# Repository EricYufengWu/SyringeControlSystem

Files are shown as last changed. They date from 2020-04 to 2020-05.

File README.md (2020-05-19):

# Syringe Control System for Soft Robot Actuators

Demo

## General Info

This repository hosts code, PCB designs, and other results from my undergraduate independent research course. This research is supervised by Professor Chris Rogers at Tufts University.

The goal of the research is to develop a low-cost, modular pneumatic system that controls soft actuators using a linear actuator and a medical syringe. If time allows, I will also try to perform a well-rounded comparison between my new system and traditional controlling methods like [this one.](https://softroboticstoolkit.com/book/control-board). For now, the system is named "Syringe Control System", or SCS in short.

I would like to thank Professor Chris Rogers, Part-time Lecturer Brandon Stafford, and many other people from [Tufts Center for Engineering Education and Outreach](https://ceeo.tufts.edu/) and [Tufts Nolop FAST Facility](https://nolop.org/) for making this project possible.

Scroll down for pictures, demos, and complete building instructions.

Questions? Email yufeng.wu@tufts.edu and I will try to get back to you ASAP. I would also love to hear feedback or suggestions on how I can improve the current system.

## Images & Demos

Check out my presentation video on Youtube: https://youtu.be/lQ8lNfzFreA

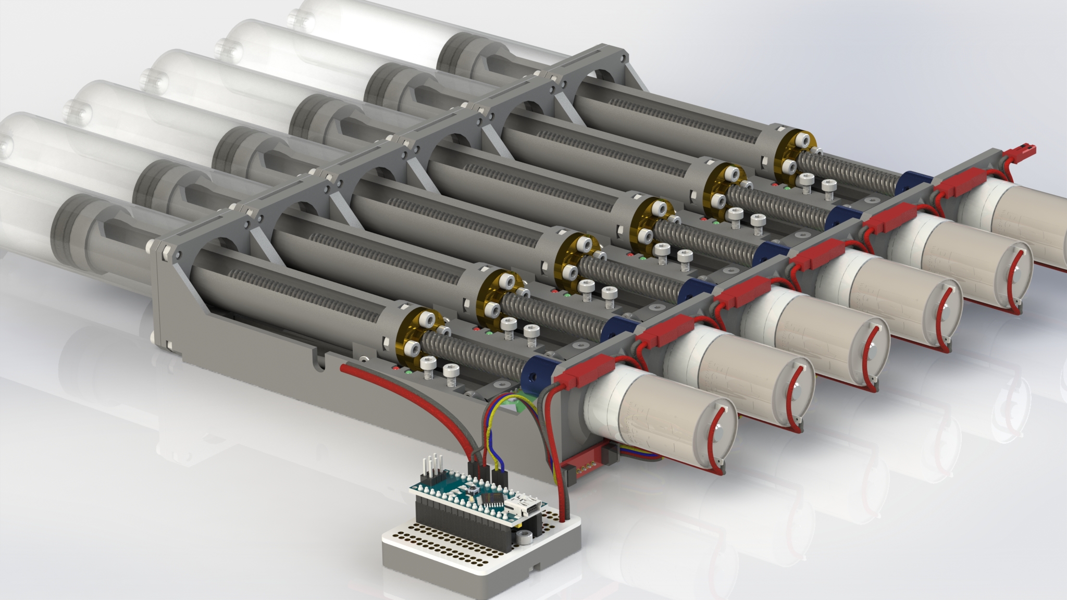
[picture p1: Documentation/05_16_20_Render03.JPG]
Rendering 01

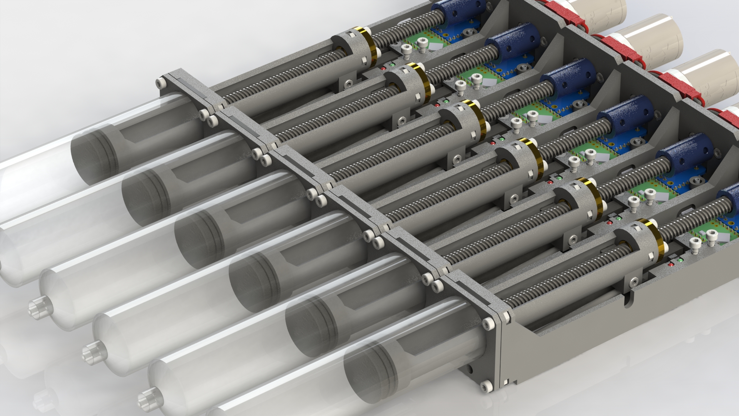
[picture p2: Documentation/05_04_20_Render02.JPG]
Rendering 02

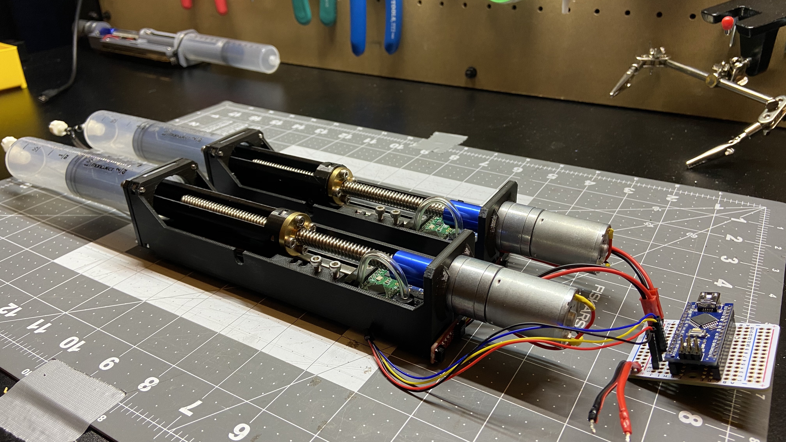
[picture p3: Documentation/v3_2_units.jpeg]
Working Demo


## BOM & Links

Click [here](https://docs.google.com/spreadsheets/d/1QlE3OmNmio2WvQ-pDKSaTucrADuNShoU5-5D75yimro/edit?usp=sharing) for the complete bill of materials.

Click [here](https://grabcad.com/library/linear-syringe-system-for-controlling-soft-robot-actuators-1/details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) for the 3D-printed components in STL, STEP, and SolidWorks format.

You can also view the 3D-model online through [here](https://autode.sk/2SUinZA)

Get the latest Gerber package and original KiCAD files (with custom libraries) under the "PCB" folder.

## Building Instructions

A full manual, including instructions on BOM, 3D-printing, ordering PCB, mechanical assembly, coding, and operation, can be found [here](https://github.com/EricYufengWu/PneumaticSyringeSystem/blob/master/Documentation/SCS_Manual_v3.1.pdf) in PDF. 

## Using The Code

Please see "Arduino_TeensyLC" for some simple demo code I wrote for the system.

Follow the instruction on the [PJRC Website](https://www.pjrc.com/teensy/teensyLC.html) to set up your Teensy LC. Similarly, go to the [Arduino Website](https://www.arduino.cc/en/Guide/ArduinoNano) if you are setting up an Arduino Nano as the Master Unit.

Upload "mid_master_TC" to the Teensy LC on each of your units. For every new unit, you will need to change the I2C slave address on line 41. If you are not sure what address values you can use, check out [this helpful list](https://learn.adafruit.com/i2c-addresses/the-list) form Adafruit. In the code, you can also tune the gain constants for the closed-loop control system in line 32 - 38. They have not been fine tuned yet, but for now they seem to work with little to no problem. If you end up finding better constant values, please do not hesitate to share it with me!

After you upload the code to a control unit, the unit should be operational in manual mode, i.e. after connecting the unit to 12V motor and 5V logic power, you should be able to control the unit using the built'in buttons. You should also be able to view the current pressure and positional data if you access the Teensy LC using a serial manitor on your computer.

Upload "top_master_nano.ino" to your arduino Nano as the master unit. You can use the serial input to send command to and get data from any designated unit in the I2C bus.

For more detailed instruciton, please refer to the instruction manual.

BEFORE YOU PROCEED: Please read the next section about the limitations of the SCS as well as things to keep in mind during its operation. 

## Limitations and Precautions
I2C protocol is capable of connecting more than 100 slaves at once. However, for the current version, it is recommended that you do not connect more than 8 units to the same master unit at the same time. This is due to the current rating of the wires used in the design. Future development will focus on how to tackle this issue.

Although the system uses Sparkfun's Qwiic system to communicaate with the units via I2C, it is currently NOT compatible with other boards on the Qwiic system: The SCS uses 5V on its logic line to power the Teensy LC, whereas the real Qwiic system uses 3.3V to power the sensors. Connecting other 3.3V sensors to the SCS system could permanently damage your sensors!

Keep in mind that although the system proves to be safe to operate, the stability of the system has not been so thoroughly tested. This mostly means that certain components might accidentally malfunction or get heated up.

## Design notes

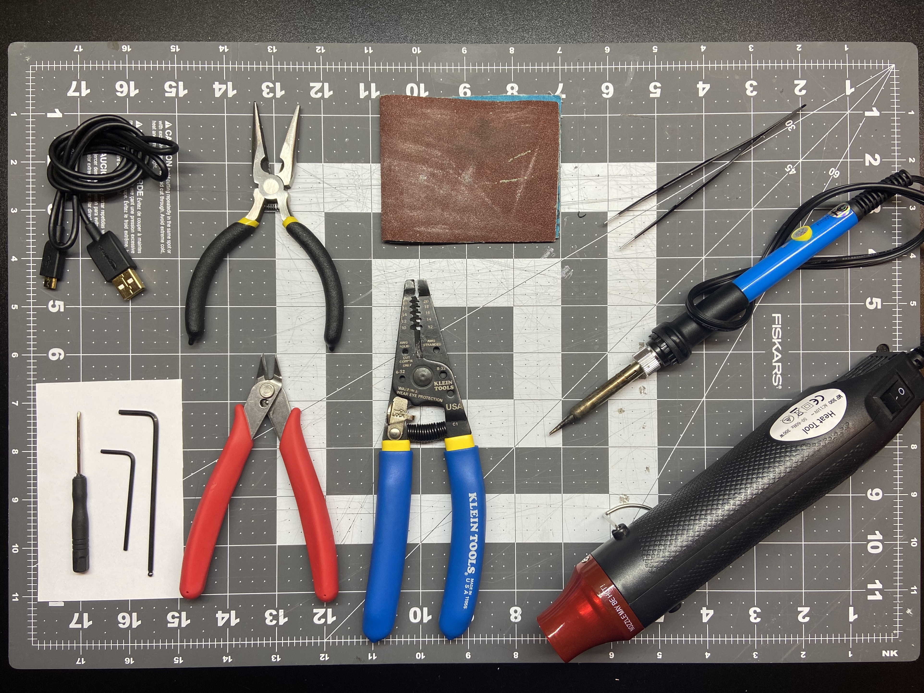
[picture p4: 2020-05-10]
Documentation/Tools_needed.jpeg

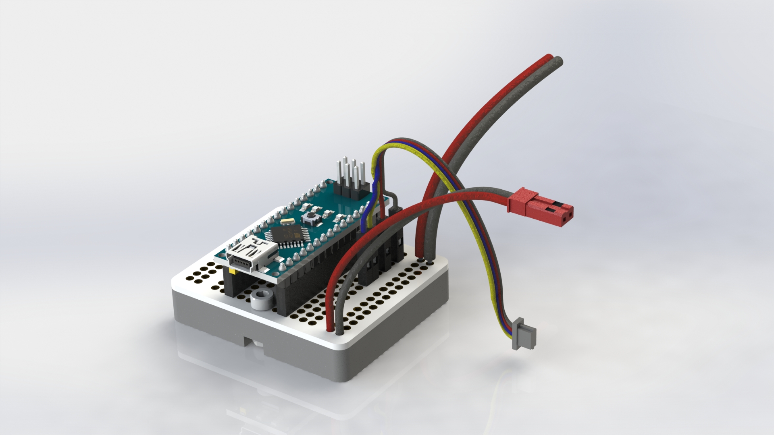
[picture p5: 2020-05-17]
Documentation/05_16_20_Render01.JPG

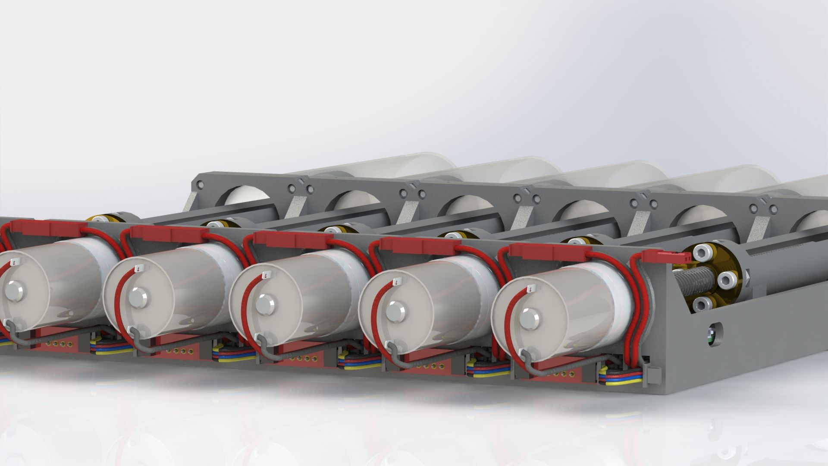
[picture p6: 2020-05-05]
Documentation/05_04_20_Render01.JPG

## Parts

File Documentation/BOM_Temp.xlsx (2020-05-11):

Item Name | Item Link | Unit Price | Item Qty | Total Price (No Shipping) | Total Price (4 units) | 500.86
Mechanical
12V motor MP #3227 | https://www.pololu.com/product/3227 | 19.95 | 4 | 79.8
4mm to 8mm shaft coupling | https://www.amazon.com/uxcell-Aluminium-Coupling-Connector-Electric/dp/B01B5QSIEW | 4.09 | 4 | 16.36
PLA filament | https://www.mcmaster.com/1317n73 | 45 | 1 | 45
M3 Flat Head 5mm | https://www.mcmaster.com/92125a125 | 3.89 | 1 | 3.89
M3 Socket Head 5mm | https://www.mcmaster.com/91292a110 | 4.97 | 1 | 4.97
M3 Socket Head 10mm | https://www.mcmaster.com/91292A113 | 4.97 | 1 | 4.97
M3 Socket Head 16mm | https://www.mcmaster.com/91292a115 | 5.87 | 1 | 5.87
M3 Hex Nuts | https://www.mcmaster.com/91828a211 | 5.55 | 1 | 5.55
M2 Button Head Screw 4mm | https://www.mcmaster.com/92095a451 | 4.12 | 1 | 4.12
Electrical
Teensy LC | https://www.digikey.com/product-detail/en/sparkfun-electronics/DEV-13305/1568-1233-ND/5721428 | 14.38 | 4 | 57.52
Motor Driver DRV8871 | https://www.digikey.com/products/en?mpart=3190&v=1528 | 7.5 | 4 | 30
Adafruit MPRLS Pressure Sensor | https://www.digikey.com/products/en?mpart=3965&v=1528 | 14.95 | 4 | 59.8
Short M-Header | https://www.digikey.com/product-detail/en/adafruit-industries-llc/4173/1528-2946-ND/10130488 | 0.75 | 6 | 4.5
Short F-Header | https://www.digikey.com/product-detail/en/adafruit-industries-llc/4174/1528-2947-ND/10130489 | 1.25 | 6 | 7.5
Linear Potentiometer | https://www.digikey.com/product-detail/en/tt-electronics-bi/PS100-2B1AR10K/987-1407-ND/2620676 | 5.49 | 4 | 21.96
Mini Push Buttons | https://www.pololu.com/product/1400 | 0.99 | 2 | 1.98
Right Angle M-Header | https://www.pololu.com/product/967 | 0.99 | 1 | 0.99
Qwiic I2C Breakout | https://www.sparkfun.com/products/14495 | 1.5 | 5 | 7.5
Qwiic to M-Jumper | https://www.sparkfun.com/products/14425 | 1.5 | 1 | 1.5
Qwiic 50cm Cable | https://www.sparkfun.com/products/14426 | 0.95 | 5 | 4.75
Green LED 3mm | https://www.sparkfun.com/products/9650 | 0.35 | 1 | 0.35
Red LED 3mm | https://www.sparkfun.com/products/533 | 0.35 | 1 | 0.35
Resistor 100 ohm | https://www.sparkfun.com/products/14493 | 1.2 | 1 | 1.2
Resistor 330 ohm | https://www.sparkfun.com/products/14490 | 0.95 | 1 | 0.95
16 AWG Wire | https://www.amazon.com/TYUMEN-Electrical-Extension-Flexible-Lighting/dp/B07SG23DT1 | 17.99 | 1 | 17.99
20 AWG Wire | https://www.amazon.com/BNTECHGO-Silicone-Flexible-Strands-Stranded/dp/B01F8PO5XE | 11.99 | 1 | 11.99
Heat Shrink Set | https://www.amazon.com/560PCS-Heat-Shrink-Tubing-Eventronic/dp/B072PCQ2LW | 7.99 | 1 | 7.99
PCBs | https://oshpark.com/ | 45.4 | 1 | 45.4
Pneumatic
Syringe | https://www.mcmaster.com/7510a802 | 3.13 | 4 | 12.52
Male Luer to 3/32'' | https://www.mcmaster.com/51525k212 | 3.78 | 1 | 3.78
Female Luer to 3/32'' | https://www.mcmaster.com/51525k122 | 4.27 | 1 | 4.27
3/32'' Y connector | https://www.mcmaster.com/5463k52 | 7.96 | 1 | 7.96
3/32'' Tubing | https://www.mcmaster.com/5233k92 | 15 | 1 | 15
PTFE Sealing Tape | https://www.mcmaster.com/6802k18 | 2.58 | 1 | 2.58
Other Tools Needed
Breadboards
Jumper Wires
Multi-meter
Heat Gun
Soldering Station
Wire Cutters
Precision Plier
Flush Cutter
X-Acto Knife
Benchtop Power Supply
Sand Paper
Screw-drivers or Allen Keys
3D-printer
Some Wires

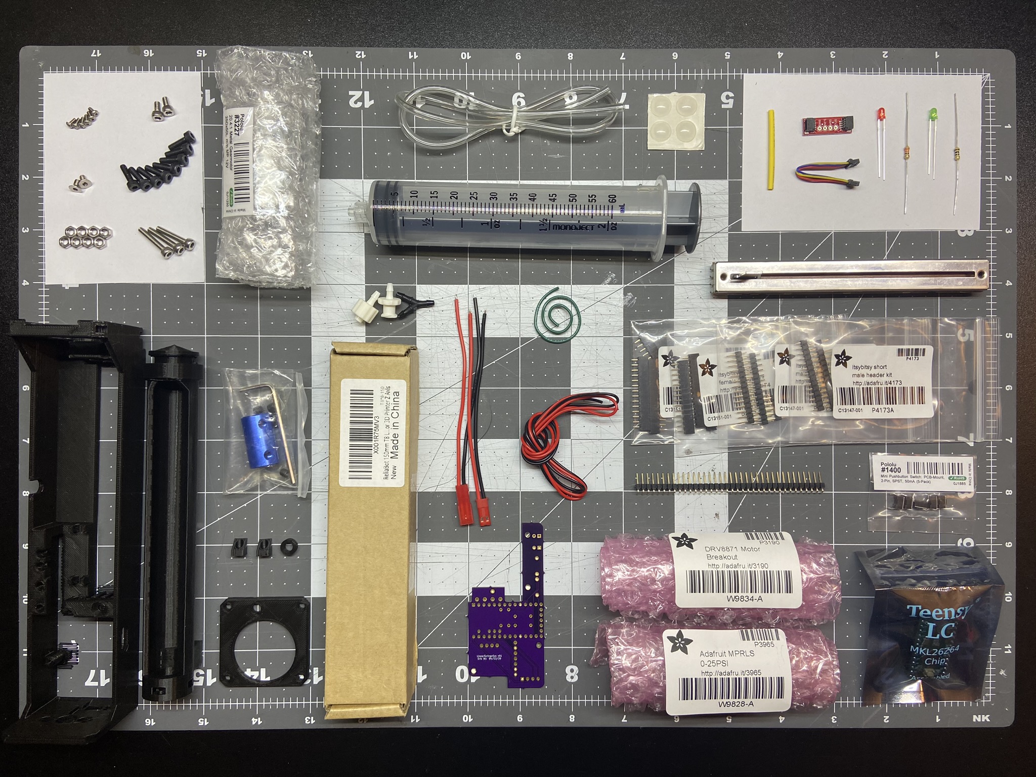
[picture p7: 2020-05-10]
Documentation/Material_1.jpeg

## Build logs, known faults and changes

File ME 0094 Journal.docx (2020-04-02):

Jan 14th, 2020

Rough Plan:

- Step 1: LEGO actuator + small syringe,
  - powered by LEGO Technic block with simple forward/reverse option
  - manual air release with switch
  - goal: explore possibility of using low-cost, easily-accessible components to control soft robot actuators.
- Step 2: Stepper motor + medium/large syringe
  - Powered by Arduino/raspberry pi with ability to hold at exact position
  - Manual/automatic air release
  - Pressure sensor in line & display readings or become part of the control algorithm
  - Goal: to produce more stable and precise pressure output
- Step 3: Compare step 1 & 2 with existing control system (pump + solenoid valves)
- Step 4: using step 1 or step 2 to create a demo with multiple channels (snake, tentacle, articulated fingers etc.)
- Step 5: (if time allows) ultimate strength challenge
  - Fabricate a custom syringe at Bray (aluminum etc.)
  - Use a heavy-duty linear actuator with feedback
  - Test the performance on an artificial air muscle

To do: Look up ferromagnetic materials

Links:

LEGO Linear Actuator: https://www.amazon.com/Lego-Technics-Linear-Actuator-61927C01/dp/B014T9E43G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

Stepper motors:

Heavy-duty Linear Act.: https://www.pololu.com/category/127/linear-actuators

Syringes:

Pressure Sensor:

Jan 22nd, 2020

- Performed research on existing control mechanism for soft actuators.
  - In most cases, hard valves and pumps are still widely used for controlling soft actuators:
    - https://softroboticstoolkit.com/book/control-board

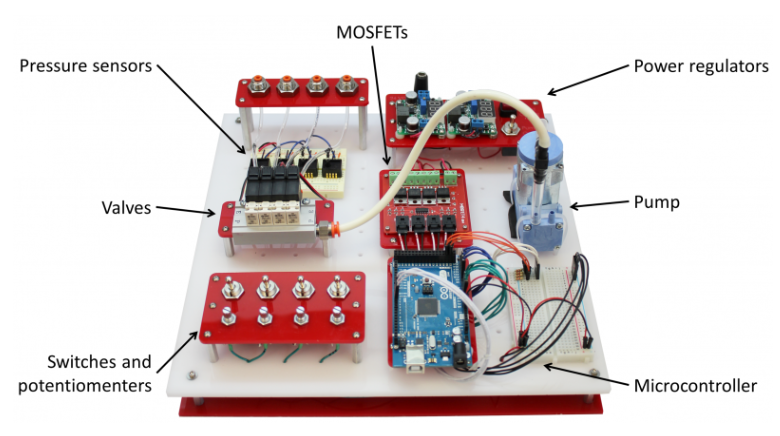
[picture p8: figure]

This is a traditional control system presented by Soft Robotics Toolkit and is open-source. Similar set up is also used by NASA: https://www.nasa.gov/feature/langley/beyond-the-metal-investigating-soft-robots-at-nasa-langley

  - A research group recently published a paper about making a custom-made, soft, bistable valve to replace the hard solenoid valves: https://robotics.sciencemag.org/content/3/16/eaar7986/tab-pdf
  - Useful paper that summarizes current soft robotics manufacturing and control systems: https://www.nature.com/articles/nature14543.pdf
  - ***Found this useful research paper on using force-feedback and the pressure-feedback controllers to actuate the SRAs reliably. https://www.ncbi.nlm.nih.gov/pmc/articles/PMC6545483/pdf/nihms-1027456.pdf

Based on research, it seems a promising direction for my research is to build a syringe pneumatic/hydraulic system that uses force-feedback or pressure-feedback controllers to actuate soft robot actuators.

**Q Has anyone used the linear actuator with EV3?

- Submitted purchase request for some LEGO linear actuators
- Next Steps:
  - build the actuator in LEGO version
  - review the research paper and learn control
  - start designing version one of my syringe system and produce a BOM

Jan 26th, 2020

- Found this 3d-printed linear rail for syringes - https://www.youtube.com/watch?v=Q3A4NqTPOYY

Might be useful as reference when I design my setup.

Jan 27th, 2020

- Used a linear actuator, The MINDSTORMS EV3 kit, and a syringe to build a prototype setup for the LEGO version of the system. The linear actuator is directly mounted to a LEGO medium motor, which is then controlled by the brick with VSC and micro-python.
- The setup was able to control the linear motion of the syringe to some degree, however:
  - The structural integrity of the LEGO build and the torque provided by a single linear actuator is not ideal. The next step could be to mirror the build at the opposite side with another linear actuator to double the force and make the setup Stabler.
  - The LEGO linear actuator does not have a large stroke width. Will need to try with actuators to confirm this.

Jan 30th, 2020

- Found a research journal about developing a soft robot using ferromagnetic materials: https://www.researchgate.net/publication/335455581_Ferromagnetic_soft_continuum_robots
- Reason not to focus in this direction:
  - Not realistic with current available resources, time, and scope of the independent studies
  - Focuses more on developing new types of actuation methods, whereas I’m planning to focus on improving the control method for existing, accessible, and easy-to-fabricate materials.
- Finished building the LEGO version of the syringe system with two medium motors and two linear actuators.
  - Able to control the syringe to actuate some actuators in a reasonably accurate manner
  - Proved that LEGO can control soft robotics!
- Next steps:
  - Improve/Document the current LEGO setup
  - Start designing a non-LEGO version, give design&BOM

Feb 5th, 2020

- 80% done with the Instructables on making the LEGO syringe system. Still waiting to cast a successful soft actuator and film a demo of the complete system.

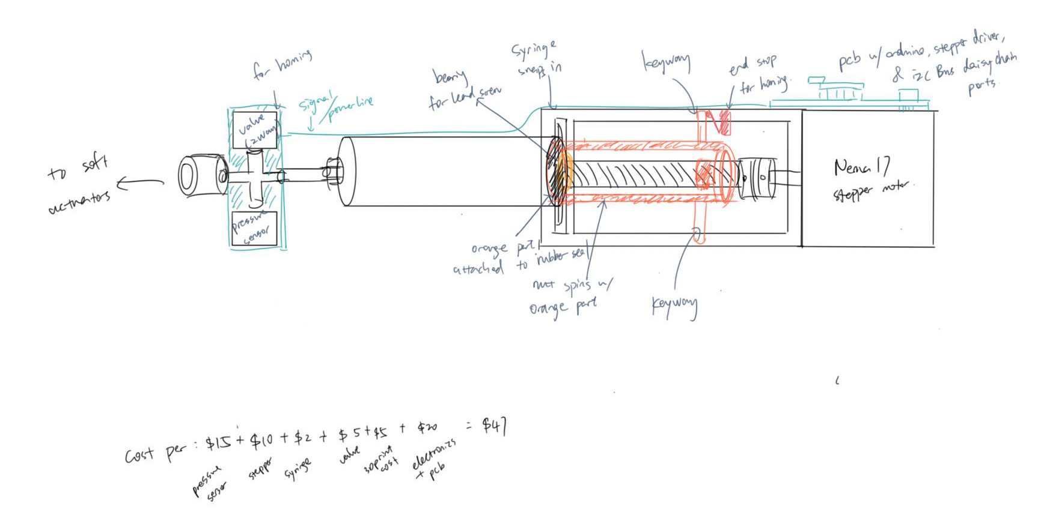
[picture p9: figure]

- Preliminary sketch done for the new, non-LEGO syringe linear actuator system:
  - Trying to limit the cost of each unit to be less than $50.
  - Ideally, each unit should have a microcontroller on board, capable of listening to an I2C bus – modularity.

Feb 9th, 2020

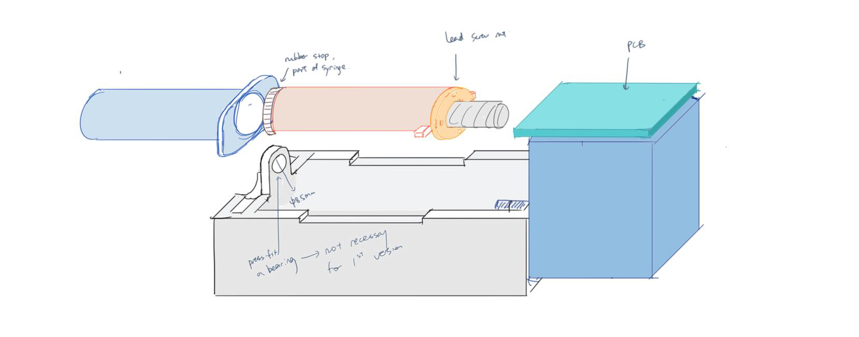
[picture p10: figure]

- Detailed Sketch
- BOM:
- Preliminary CAD with selected components:
  - Included stepper motor, shaft coupler, lead screw with nut, and syringe components

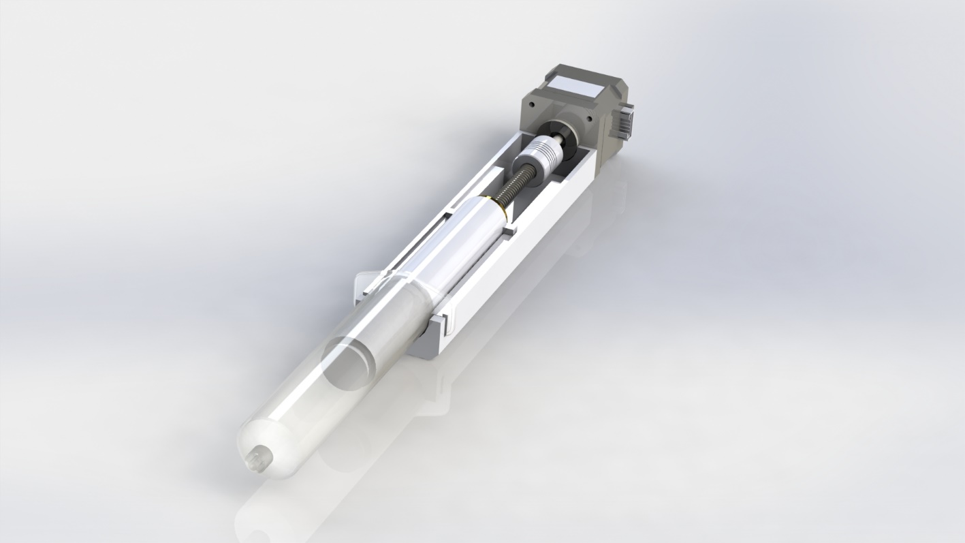
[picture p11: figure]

  - still need to add: end stop, tubing, upper shell, PCB, etc.

Feb 18th, 2020

- First Iteration of the linear actuator model has some issues:
  - It is difficult to put in the screw that are used to attach the stepper motor to the main housing
  - The syringe lip was a little loose when attached
- Updated the CAD model in SolidWorks, and hopefully I can print the next version soon.
  - I was also trying to incorporate end stops to the bottom_housing model. Found this compact end stop module made for 3D printers, but will suit my purpose:

https://www.amazon.com/Printer-Accessories-Mechanical-Endstops-MXRS/dp/B083BZ3VTL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

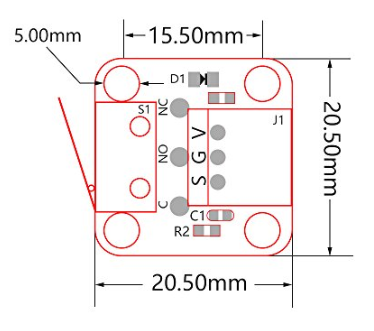
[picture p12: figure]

This end stop converts touch sensor data to digital high, so I can directly plug it in a micro-controller, no need for pull-down resistor.

Feb 22nd, 2020

- 3D-printed out and assembled the first version of the syringe system. Assembled the components – except for the end stop and the pressure sensor, which I’m still waiting for to arrive in a few days. Right now, the system looks pretty good. Some following steps:
  - Connect the end stop module, pick a stepper motor driver, and breadboard the electronics for testing the syringe
  - The end support for the lead screw appears to be a little tight. Consider inserting a bearing or simply increase the diameter for the next iteration.
  - Design a 4-way connector that will be attached to the end of the syringe, which allows connection to a valve, a pressure sensor, and the actuator.

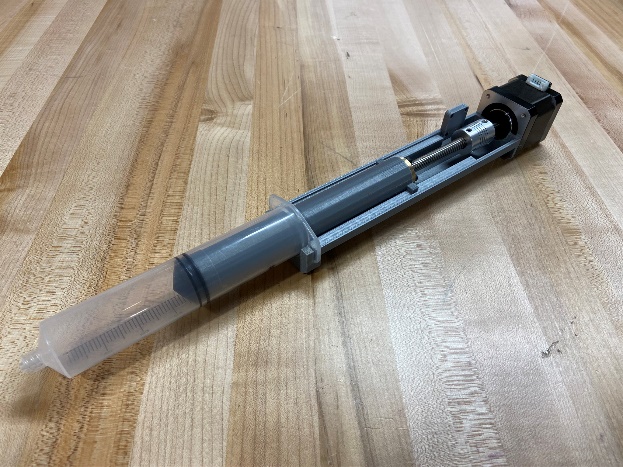
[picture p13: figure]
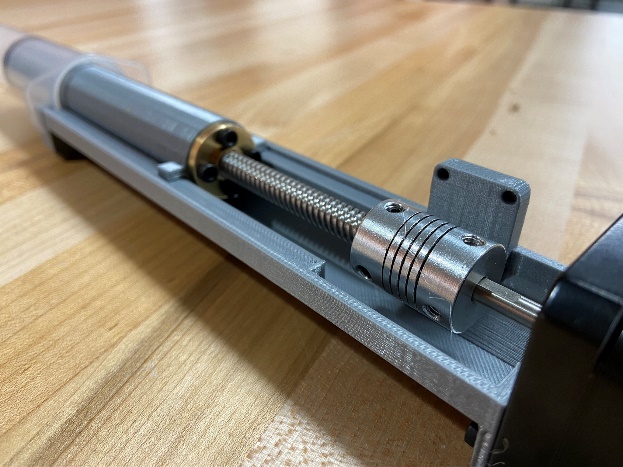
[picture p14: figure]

Feb 27th, 2020

- The pressure sensor, solenoid valve, and the end stops have arrived. Some issues that are currently preventing me from moving forward:
  - The end stop does not fit in the assembly the way id did in SolidWorks – the solder joints are thicker than my estimation. Will have to make changes in the design, moving the module to another location
  - The pressure sensor and the solenoid valve are a little bigger than I expected. Will see if I can still incorporate them while maintaining the modularity of each units.
- Now that I’m starting to think about controlling the motor, here’s a qualitative schematic

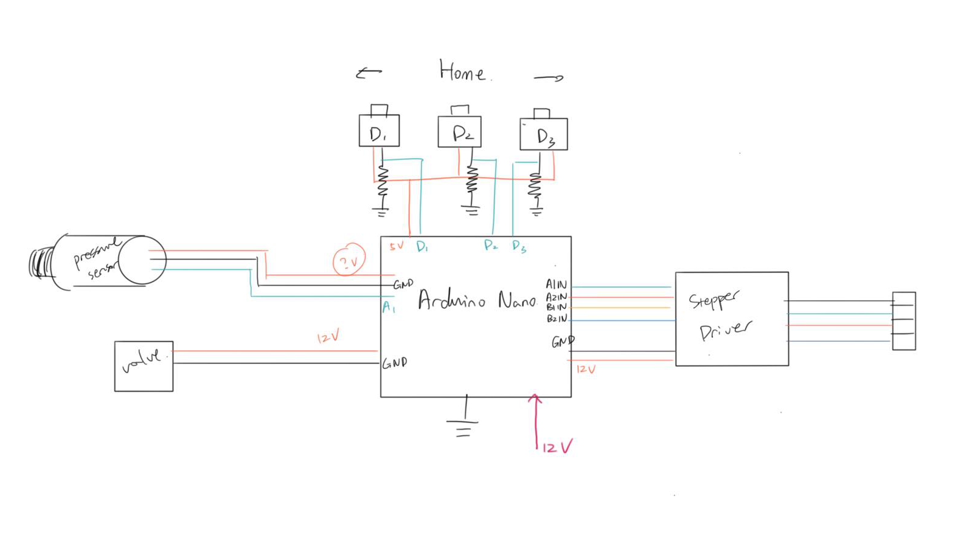
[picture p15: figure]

March 3rd 2020

- Second version of base body: End stop fits in, but the flanged nut would hit the main switch body, deforming the touch switch before the switch can be activated. Solution: Modeled in an attachment piece onto the middle piston, so the piston will flush with the flange.
- The top attachment to the stepper motor forms an angle relative to the base-added another screw from bottom of the base to connect the two components together
- My plan for the following weeks:
  - Finish making a single model
  - Reach out to Steve Cogger (through Chris) after having the system tested on a breadboard.
    - Will need to decide between usb serial and I2C. Leaning towards I2C because the need to stack the modules together, and expand the possibility for advanced users to customize and integrate the system to their existing Arduino/hardware projects
  - Develop testing protocols to compare a single syringe module and a valve system
    - Compare the time response of both models
    - Noise level at performing specific tasks (e.g. incrementing pressure steps, holding at a specific pressure level, etc.)
    - Operation to failure of valves vs syringes (for valve – limited lifetime, for the syringe – likely to be much longer)
    - Maximum pressure output (might be more of a challenge to the syringe system
    - …

March 5th, 2020

- 3D-printed and assembled the next iteration of the end stop + base + lead screw. Below is a series of images showing the assembly design:

Had to print an extra extension piece to make the center piston align with the end of the flanged lead screw nut, so that the end stop will fully engage at the current position.

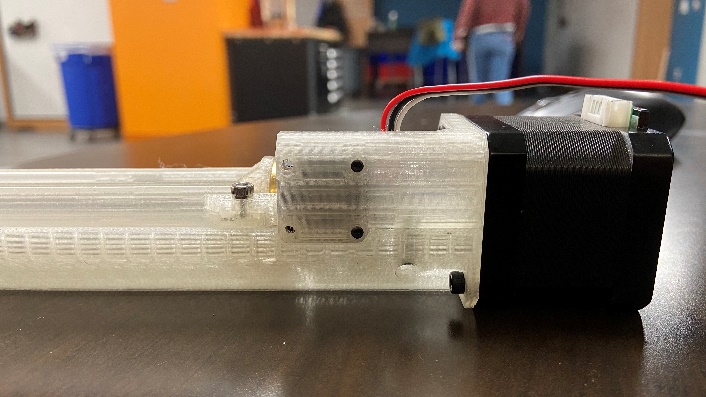
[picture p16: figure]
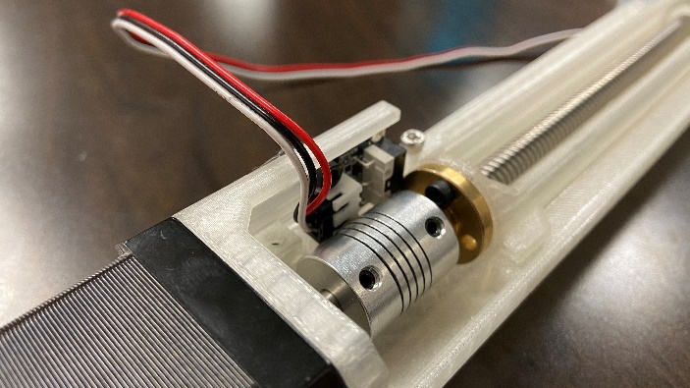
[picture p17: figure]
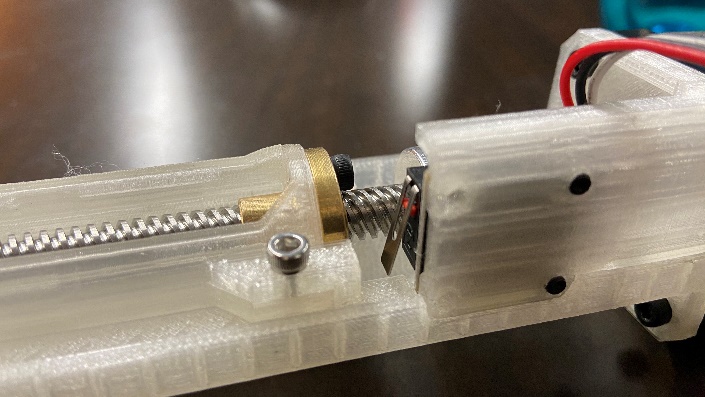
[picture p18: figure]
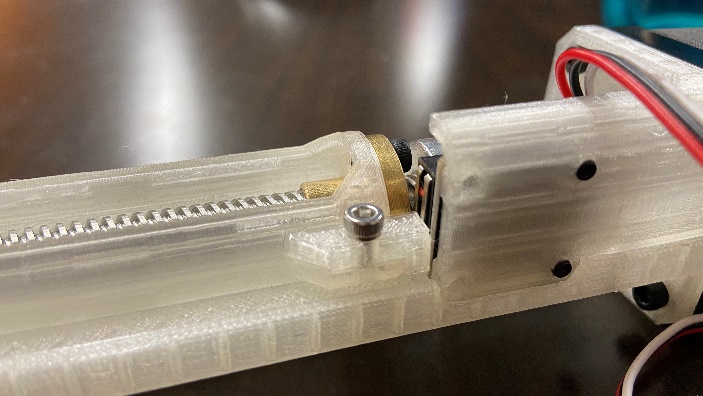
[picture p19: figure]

Chris also suggested that I try a linear potentiometer. I might look into buying one to test it out, but there are a few concerns I have regarding the linear pot:

  - The size of the linear potentiometers is rather fixed – might be a little too big for the current design
  - Length – again, might end up too long/too short
  - One way to solve the last two issues is with a custom-made linear potentiometer, but it might end up not being as reliable and will take up longer time.

March 9th, 2020

- Found a different type of pressure sensor:
  - Link: https://www.digikey.com/product-detail/en/nxp-usa-inc/MPXV7002DP/MPXV7002DP-ND/1168436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
  - Advantage: compact and relatively cheap. Available on digikey as an SMD part. Might ask Chris to order one to play with and see if this can replace the big, bulky pressure sensor
- As for update regarding the solenoid valve and how it can be integrated:
  - Considering to instead have the 3d-printed piece have a hose nozzle output, so that users can decide whether they want a cheap manual valve or an integrated solenoid valve (will leave a place for the valve control in the pcb.)
  - Next is to perform iteration on 3d printers to find the optimal tolerance for luer lock and other related dimensions

March 10th, 2020

- Rapid prototyping on the Prusa MK3S 3D printer resulted in a working model of low-cost luer lock.
- Found a possible alternative to the solenoid valve system: 4-way stopcock:

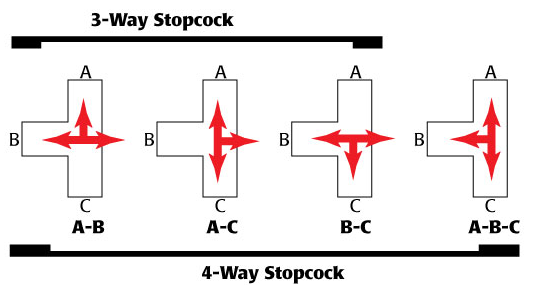
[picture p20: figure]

Possible vendors:

https://www.vitalitymedical.com/hi-flo-four-way-stopcock.html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

https://serfinitymedical.com/products/discofix-stopcock-4-way-b-braun-456020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

  - As seen from the image, I could connect C to the syringe, and A to actuator + pressure sensor. Configuration #2 is the operation mode, and configuration #4 is the calibration mode.
  - For the final setup, this could be a simple add-on to the system. The user can choose to directly connect the 3D-printed connector I designed that splits into the actuator and pressure sensor connection; alternatively, they could choose to purchase this and simply add the 4-way stopcock inline to make the calibration process easier to perform.

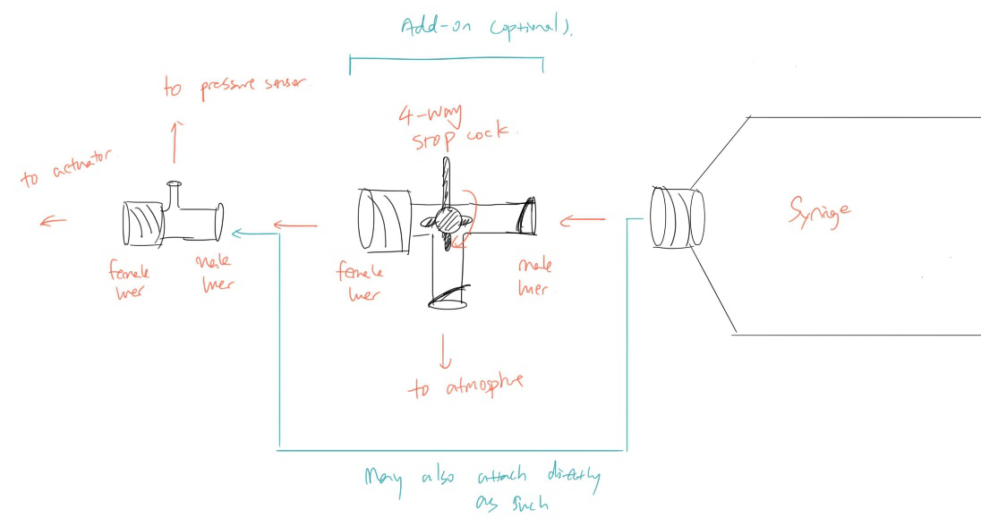
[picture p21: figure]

- Considering bringing back the Adafruit I2C pressure sensor – other options are wither two clumsy, too expensive, or does not have desirable pressure range.
  - Will validate this decision by testing the Adafruit pressure sensor and the NPT pressure sensor with the gripper actuator
- * Top priority is still finishing the open-loop system with the stepper motor and the syringe.

March 11th, 2020

- Campus will shutdown doe to Coronovirus. Will need to come up with a plan

Week of March 9th | Finalize the physical design the best way I can Try and solve the stepper motor vibration issue Breadboard manual control system with buttons
Week of March 16th | Take some rest…? Use the manual control system to test out different pressure sensors. Pick a pressure sensor.
Week of March 23rd | (if needed, figure out soft I2C/ possibility to use an Arduino as both a master and a slave)
Week of March 30th | Close-loop system with pressure sensor in line with syringe and actuator
Week of April 6th | Continue working on single close-loop system Start developing I2C code for master Arduino/Pi and individual Arduinos.
Week of April 13th | Continue developing I2C code for master Arduino/Pi and individual Arduinos.
Week of April 20th | Acquire performance data and compare with air pump.
Week of April 27th | Acquire performance data and compare with air pump. Organize research results and prepare for potential presentations.
Week of May 4th

Will mostly need (and might be able to get):

A soldering station

Jumper wires, resistors, capacitors, other electronics. Various pre-made boards from Adafruit/Pololu etc.

PCB manufacturing service

Nscope

March 21st, 2020

- A little behind the schedule, mostly dealing with COVID-19 related issues. Hope to resume research starting today.
- Revisited previous breadboard setup where the stepper motor is vibrating and creates unpleasant sound.
  - Tried adding different capacitors to reduce current spikes
  - Searched online to try to find solutions
  - Reduced some vibration noises by applying hot glue to loosen parts on the end stop module
  - Considering replacing the flexible shaft coupling to spider-style/normal coupling to reduce noise and size. Some viable options include:
    - https://www.amazon.com/ZYCST-Aluminium-Coupling-Connector-Airplane/dp/B07QPKGM1Q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
    - https://www.amazon.com/Befenybay-Aluminium-Flexible-Coupling-Connector/dp/B07RMZCLZ3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
- The stepper motor, unfortunately, was not delivering enough torque. It started skipping once out of a few steps as pressure increases. It still pushed the syringe all the way to the end, but skipping steps made it hard to monitor the position. Possible solutions I can think of:
  - Ignore the step-skipping, and use a linear potentiometer to monitor the position
  - Use a stronger stepper motor
  - Use a DC motor with encoder (or without?) and use either two endstops or a linear potentiometer
  - Use a brushless motor…? Maybe see if O-drive has an open-source schematic…
- Motor RPM to linear actuator moving speed:
  - Lead screw: 2mm pitch, 4 starts
  - 1 revolution of motor – 8mm travel of lead screw.
  - Travel speed (mm/sec) = (RPM / 60) * 8mm
  - Current speed with 17HS19-2004S1: approx.. 16mm/s; therefore, to find a DC motor that matches the speed, I should be looking for a motor with RPM > 120. Ideally the higher the better, with enough torque and reasonable rated voltage and current draw.
- Next steps:
  - Prototype a connector with female luer, male luer, and a tube coming out – then hook up a pressure sensor in line with the syringe, and use a scale found in my house to graph a pressure-torque characteristic of the motor.
  - Pick a desirable maximum pressure and a corresponding force. Calculate the torque needed for the motor. Use this as the final criteria in selecting a motor (maybe with a factor of safety of about 1.5?).
    - https://www.pololu.com/category/115/25d-metal-gearmotors
    - https://www.pololu.com/category/116/37d-metal-gearmotors
  - Look for linear potentiometers (100mm travel length).
    - https://www.digikey.com/product-detail/en/tt-electronics-bi/PS100-2B1AR10K/987-1407-ND/2620676
    - Might need a larger syringe since the travel length is now limited: https://www.amazon.com/DEPEPE-Connections-Scientific-Measuring-Filtration/dp/B07PPFLKRD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

March 22nd, 2020

- Prototyping of the Y Luer connector hit a bottleneck – the pla isn’t strong enough and does not produce an air-tight environment. The pisture shows the iterations I performed today:

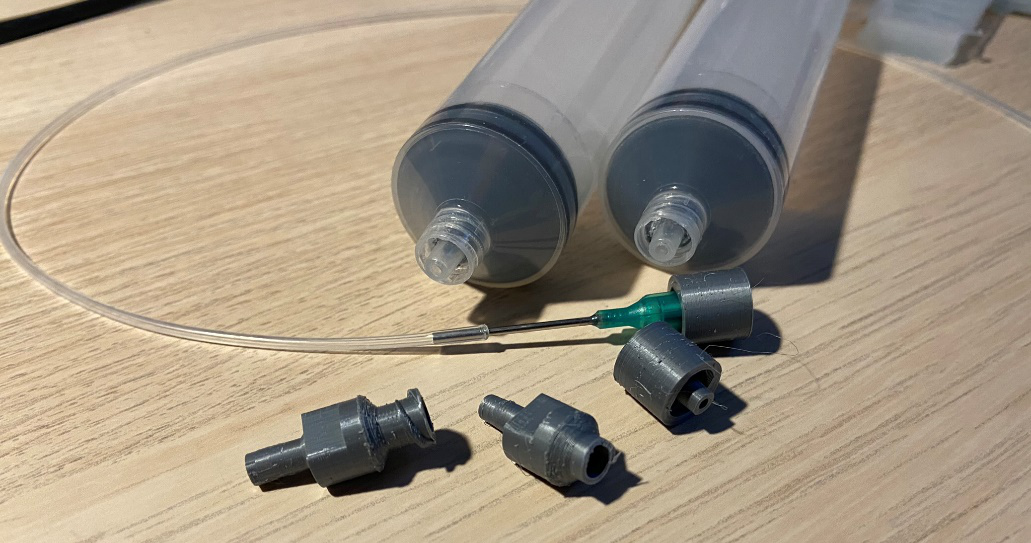
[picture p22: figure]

The PLA wasn’t strong enough – as I tried to untwist the connector off from the syringe, the end broke off and stayed inside the luer connector, making the syringe unusable.

Some options includes:

  - Teflon Tape
  - Use petg/or other PLA substitute
  - Use industrial Luer connectors instead (promising)

So the current plan would be:

  - Purchase some y-connector, and while waiting for the shipment, I could also purchase some PETG and Teflon Tape. In the best scenario, both methods would work and I can present more alternatives of my design in the final report. I hope that through this process, at least one of the options would work.
  - https://www.qosina.com/y-connector-male-luer-connector-with-spin-lock-two-female-luer-lock-ports-84044

https://www.mcmaster.com/51525k122

use 3/32 ID Tubing in the pressure line. Solved the problem!

- To do:
  - Start compiling an order list for CEEO
  - Use the scale to roughly measure the pressure-force relation
  - Use the relation to predict the force needed to actuate the example gripper design
  - Calculate the required force/torque of motor. Pick a new motor and re-design.

March 23rd, 2020

- 60ml Syringe Pressure-Force Characteristic Test. Method: I placed the end of the syringe on a kitchen scale, with the pressure sensor hooked up to the other side. Next to the setup, I have the Arduino Serial monitor opened, which outputs the pressure in the system in PSI.

YouTube Link (listed only): https://youtu.be/_aCKt8hK5S8

  - I chose to only graph results averaged from trial 4-6, since the frictionless syringe gives a much more linear result. The force required to get the pressure to 24 PSI (a little below the limit of the Adafruit pressure sensor) is around 39.12N.
  - I also did a test on the existing soft gripper I have by pressing the syringe to the kitchen scale in similar fashion. I performed 3 trials and ended up with a force output of around 19.77 N. From the characteristic graph, the pressure around 18.97 psi, which is well within the range of the pressure sensor.

March 25th, 2020

- Calculated the required torque based on the following video: https://youtu.be/cdDYhViYO9s

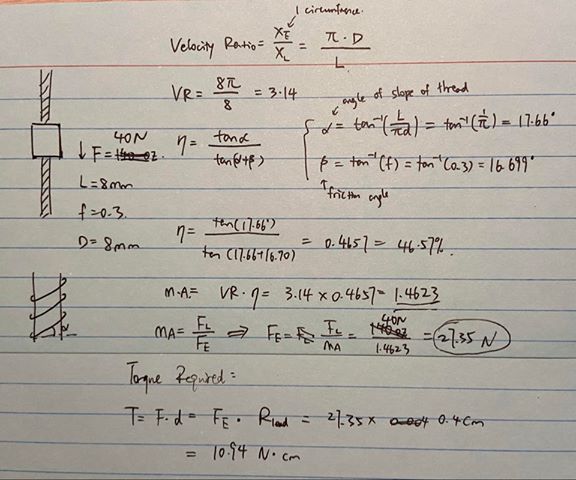
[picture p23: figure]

Interestingly, the calculation implies that only about 10.94 N*cm of Torque is needed, which is well within the “holding torque” of the stepper motor I am using. Therefore, I revisited the stepper motor setup.

  - I noticed that the friction inside the free-running syringe is partially the reason of the poor performance. I applied some cooking spray :) to the inner rubber seal and it worked a little better, but still not as close as the rated performance.
  - I then took a closer look at the driver and whether the driver is actually outputting enough current for the motor. Measuring the current through one coil gives approximately 600mA. From the A4988 Datasheet, it appears that this corresponds to a current draw of ~1A, which is less than the rated 2A of the stepper.

A4988 Datasheet: https://www.pololu.com/file/0J450/a4988_DMOS_microstepping_driver_with_translator.pdf

Pololu stepper driver instruction: https://www.youtube.com/watch?v=89BHS9hfSUk&feature=youtu.be

  - I then realized that the A4988 board I am using is different from the ones that Pololu sells – could be a knockoff, which prevents me from accurately measuring and adjusting the current limit. I already turned the on-board potentiometer all the way to the max side, so I think I’ve pushed board to its limit. I may need a better stepper driver.
  - Next, I plan to test the torque of the motor by 3D-printing a lever-arm and attach weight to the arm.
- While I am waiting for the result of the torque testing, I am debating whether I should:
  - keep using the stepper motor and hope that the new driver would solve the problem. The advantage is that most of my CAD model would remain the same, and I already have the schematic, testing code etc. set up; the downside is that this has a higher chance of not working at all in the end.
  - Switch to a DC motor based on the calculated torque and a relatively high “factor of safety”. This would take more time to implement but would have a higher chance of success; besides, DC motors are much easier to deal with than stepper motors. I will have the linear pot and pressure feedback, so precise “stepping” is no longer a necessary element to have.
  - In both cases, I need to start integrating the linear potentiometer, replace the flexible coupling and the endstop, and re-print the entire setup.

March 26th, 2020

- Some further investigation regarding the lack of torque produced by the stepper motor.
  - 3D-printed a lever arm and used a water bottle and a kitchen scale to create “standard weights” for the torque test.
  - After a series of testing, I found out that under low RPM (about 30 RPM), the motor was able to produce about 10N*cm of force, which is, coincidentally, the same as the maximum torque required to reach the pressure sensor’s upper limit. The reason I was running into skipping issue before were: a) Speed was too fast, and b) I had a bad control code for the motion (I had increments of 20 steps inside two if statements which listened to the states of two buttons)
  - However, even if The system could work right now, I’m still leaning towards the plan to switch to DC motor. Reason being that:
    - The stepper motor system is far too loud, and it vibrates like crazy…
    - The stepper motor would run at a lower operation speed at desired output torque.
    - DC motors are far easier to control, and with the linear potentiometer feedback, the precision won’t be a problem.
- New Purchase list:

Concern: Due to the pandemic most of the online sites have announced to have delayed shipping or no shipping at al. I have found suppliers for most of the components I need, except for the 4mm to 8mm couplings, which I could only find on Amazon.

- New design pared with the updated bill of materials (syringe output re-design):

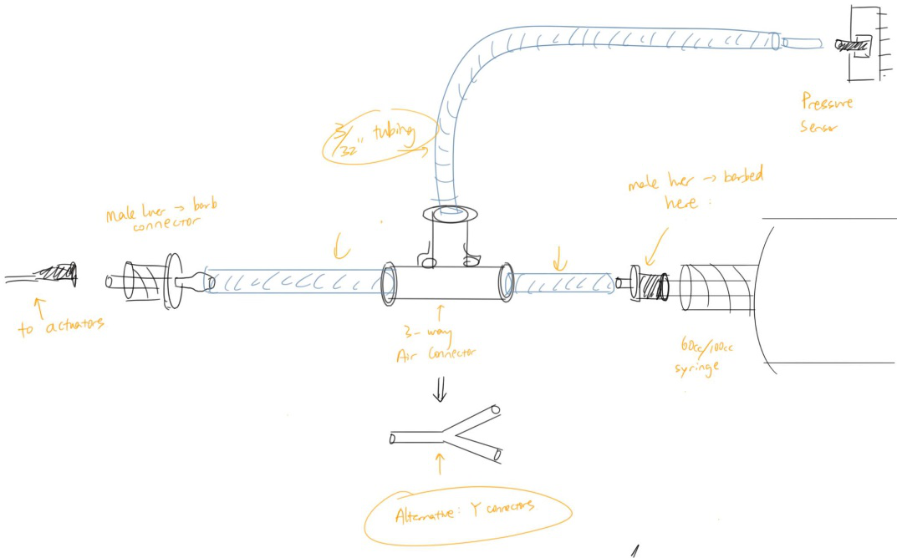
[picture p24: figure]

March 30th, 2020

- McMaster-Carr & Digi-key orders have arrived. With most of the components at hand, I organized the components, soldered some boards, and started hooking up wires for the new electromechanical system.
  - Useful links:
    - DRV8871: https://learn.adafruit.com/adafruit-drv8871-brushed-dc-motor-driver-breakout/usage
    - Linear Pot: https://www.ttelectronics.com/TTElectronics/media/ProductFiles/Potentiometers/Datasheets/PS100.pdf
    - Pressure Sensor:

https://www.digikey.com/product-detail/en/adafruit-industries-llc/3965/1528-2713-ND/9658071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

https://learn.adafruit.com/adafruit-mprls-ported-pressure-sensor-breakout

    - Teensy-LC: https://www.pjrc.com/teensy/teensyLC.html

Teensy i2c wire library: https://github.com/nox771/i2c_t3

- Outcome at the end of the day:
  - I found a modified wire library specifically designed for Teensy boards, including options to declare multiple i2c communication lines at the same time: https://github.com/nox771/i2c_t3

One difficulty I encountered is that the library for Adafruit MPRLS pressure sensor was written with the original Arduino “Wire.h” library. At the end of the day I managed to get the Teensy wire library working with the sensor by incorporating part of the code from the original header files from the Adafruit library.

  - There still exist one minor issue: Even though I tried to duplicate the original library to my best ability, the values read from the new Teensy code appears to be different from the values red from the original example code (e.g. at atm the former would read at around 6591085 while the later reads 139084.48). The values do change noticeably as pressure varies, indicating that it is the real data. I’m planning to bring this issue up in the Slack channel to see if other people have any insights.
  - With one i2c line established, I then hooked up an Arduino Nano to the other i2c channel as the “ultimate master”. With the i2c scanner I was able to detect the Teensy board at the address I specified, indicating a success in using i2c in multiple channels at the same time. I will test the system in more depth tomorrow.

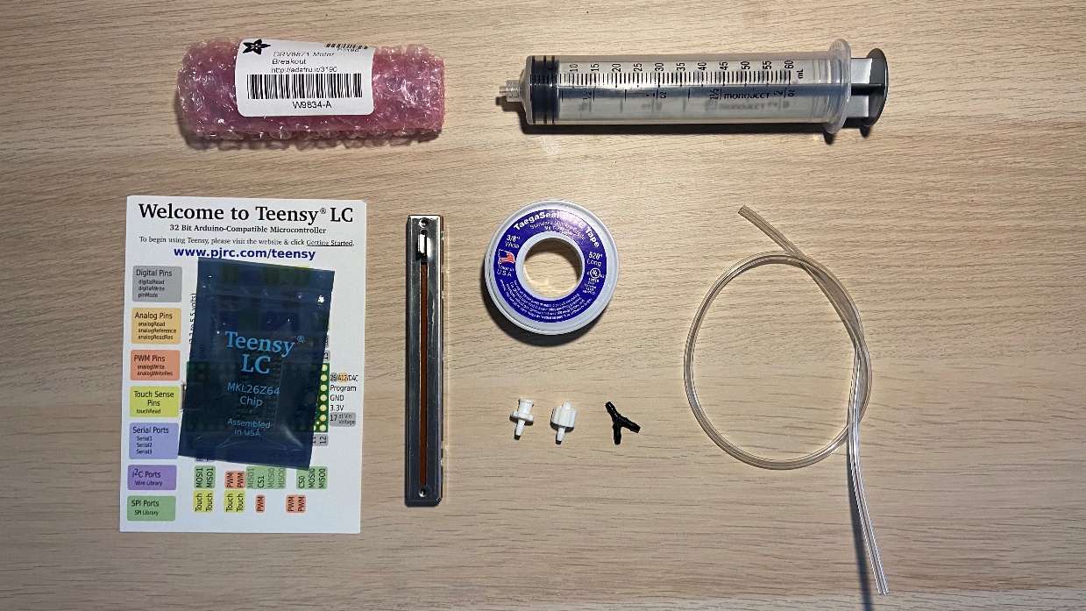
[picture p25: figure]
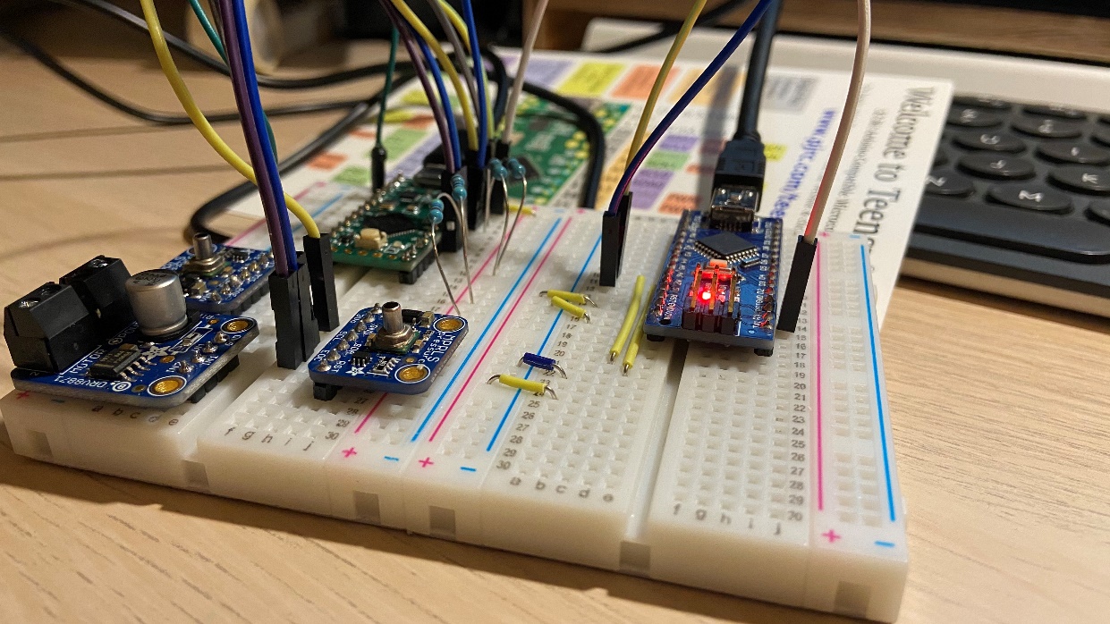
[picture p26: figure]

March 31st, 2020

- Out of serendipity (also kind hints from Chris) I solved the MPRLS reading issue by studying the datasheet of the Honeywell pressure sensor. The issue was that out of the 4 bytes of data that the sensor sent to the master, the first byte is always a status indicator. So I did an extra “Wire.read()” which would read and clear the first byte of data from the RX buffer. The last 3 bytes (24 bit) now contains the raw data which could be well-calibrated using the existing equations in the documentation (kindly provided in the Adafruit example library).
- Performed a pilot test with the y connectors, luer connectors, and the new tubing. Used the syringe to actuator the silicone gripper while taking pressure readings in the system. Video here:

https://youtu.be/JfOo434jeLU

- Finalized test code for “big master” (now an Arduino Nano) and “mid_master” (now a Teensy LC). Updated Github repo.

April 1st, 2020

- Issue:
  - Linear Potentiometer could not be red by the EV3. I tested my code by using a 10k rotational potentiometer and it worked just fine (from 1 to 1023). I checked all 5 of the linear pot I purchased from Digi-key with a voltmeter. One thing I noticed is that they are not perfectly linear – I slid it to the middle but reads around 8k…
  - Friction inside the syringe – For the old ones I have I tried vegetable oil and slide bearing grease – it seems like one of them made the rubber piston to swell, decay, crack, and the syringe unusable… Looking for suggestions (it seemed that silicone gel works pretty well?).

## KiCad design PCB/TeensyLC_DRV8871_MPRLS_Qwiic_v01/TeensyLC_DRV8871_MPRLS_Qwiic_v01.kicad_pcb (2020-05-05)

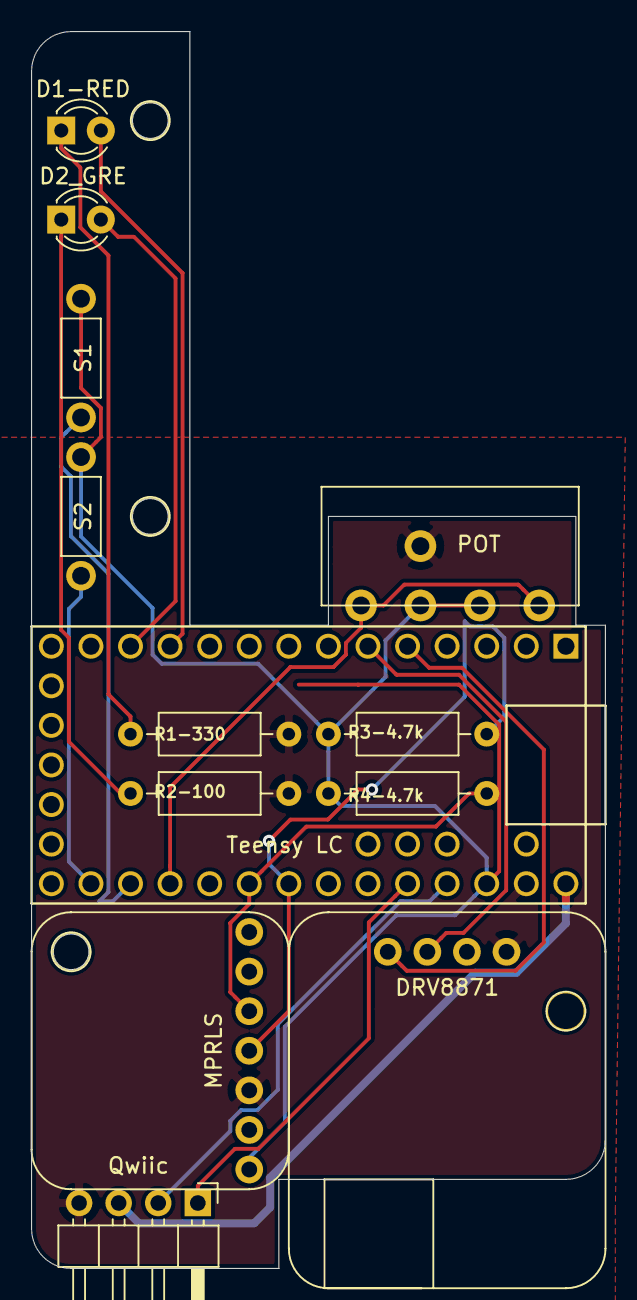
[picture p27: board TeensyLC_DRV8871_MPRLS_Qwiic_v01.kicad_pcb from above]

Board: 2 copper layers, 36.8 x 79.4 mm, 12 parts (0 on the bottom side), 6 nets.

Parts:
D1-RED, D2_GRE: LED; LED_D3.0mm
DRV8871: Adafruit_DRV8871
MPRLS: Adafruit_MPRLS; Adafruit MPRLS
POT: R_POT_US; Linear_POT
Qwiic: Sparkfun_Qwiic_Adapter; Sparkfun_Qwiic_Breakout
R1-330, R2-100: 220Ω; R_Axial_DIN0207_L6.3mm_D2.5mm_P10.16mm_Horizontal
R3-4.7k, R4-4.7k: 4.7kΩ; R_Axial_DIN0207_L6.3mm_D2.5mm_P10.16mm_Horizontal
S1, S2: Push_SW

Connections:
/3V3: MPRLS.1, POT.1, R3-4.7k.1, R4-4.7k.1, S1.2, S2.2
/SCL0: MPRLS.4, R3-4.7k.2
/SDA0: MPRLS.5, R4-4.7k.2
GND: DRV8871.4, MPRLS.3, POT.3, Qwiic.4, R1-330.2, R2-100.2
unnamed: D1-RED.1, R1-330.1
unnamed: D2_GRE.1, R2-100.1

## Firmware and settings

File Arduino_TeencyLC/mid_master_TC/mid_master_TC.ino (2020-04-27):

/* 
Pneumatic Syringe System Master Test
This is the first working code (proof of concept) for the "mid master" of the system, 
currently using a Teensy LC.
The "mid master" obtains pressure data from the MPRLS pressure sensor and sends it to the "big master"
The "mid master" will also take commands from the "big master" and performs feedback control on the syringe system
*/

#include <i2c_t3.h>
#include <math.h>

// Function prototypes
void receiveEvent(size_t count);
void requestEvent(void);

//Create a timer callback
IntervalTimer pressure_timer;
IntervalTimer position_timer;

// Memory
#define MEM_LEN 32
char databuf_Rx[MEM_LEN];
char databuf_Tx[MEM_LEN];
char psi_cmd_raw[MEM_LEN]; //stores incomming float command temporarily
char pos_cmd_raw[MEM_LEN]; //stores incomming position command temporarily
char str[MEM_LEN];

// Constants
int count;
int pos_raw;
volatile float psi = 14.77;
float kp_psi = 400;
float ki_psi = 200;
float kd_psi = 0;
float pos = 50.00;
float kp_pos = 80;
float ki_pos = 5;
float kd_pos = 2;
volatile uint8_t received;
uint8_t target = 0x18; // target Slave address
uint8_t self = 0x68; //This should be different for each unit.
boolean frwd_flag;
boolean back_flag;
typedef struct {
    boolean flag;  //
    float val;  //
} unit_cmd;
unit_cmd pressure_cmd;


// Pin pefinition
#define MOTOR_PORT_A 3
#define MOTOR_PORT_B 4
#define BUTTON_BACK 14
#define BUTTON_FWRD 15
#define POT 16
#define LED_RED 9 
#define LED_GRE 10

void setup()
{
    pinMode(LED_BUILTIN,OUTPUT);    // LED
    digitalWrite(LED_BUILTIN,LOW);  // LED off
    pinMode(MOTOR_PORT_A,OUTPUT);   // Motor PWM pins
    pinMode(MOTOR_PORT_B,OUTPUT);   // Motor PWM pins
    pinMode(BUTTON_BACK,INPUT_PULLDOWN);
    pinMode(BUTTON_FWRD,INPUT_PULLDOWN);
    pinMode(LED_RED,OUTPUT);   // Top LED (red)
    pinMode(LED_GRE,OUTPUT);   // Bottom LED (green)
    pinMode(POT,INPUT);
    analogWrite(MOTOR_PORT_A, 0);
    analogWrite(MOTOR_PORT_B, 0);
    
    // Setup for Master mode, pins 18/19, external pullups, 400kHz, 200ms default timeout
    Wire.begin(I2C_MASTER, 0x00, I2C_PINS_18_19, I2C_PULLUP_EXT, 400000);
    Wire.setDefaultTimeout(200000); // 200ms
    
    // Data init
    memset(databuf_Rx, 0, sizeof(databuf_Rx));
    count = 0;
    
    // Setup for Slave mode for data. Make sure the address is consistent at the master side!
    Wire1.begin(I2C_SLAVE, self, I2C_PINS_22_23, I2C_PULLUP_EXT, 400000);
    Wire1.setDefaultTimeout(200000); // 200ms
    
    // Register events
    Wire1.onReceive(receiveEvent);
    Wire1.onRequest(requestEvent);

    // Begin timer
    pressure_timer.begin(get_pressure, 50000);
    pressure_timer.priority(255);
//    position_timer.begin(get_pos, 50000);
//    position_timer.priority(254);

    // Turn Flags to false
    pressure_cmd.flag = false;
    
    Serial.begin(115200);   
}

void loop()
{
    if (pressure_cmd.flag == true){
        move_to_pressure(pressure_cmd.val);
    }

    frwd_flag = true;
    back_flag = true;
 
    float psi_copy;
    noInterrupts();
    psi_copy = psi;
    interrupts();
    get_pos();
//    Serial.print(pos);
//    Serial.print("\t");
    Serial.println(psi);
    
    if (pos_raw>1021 || psi < 1.00){
        back_flag = false;
        digitalWrite(LED_RED,HIGH);
    }
    else if (pos_raw<3 || psi > 25.00){
        frwd_flag = false;
        digitalWrite(LED_RED,HIGH);
    }
    else if (pos_raw<1021 && pos_raw>3 && psi < 25.00 && psi > 1.00){
        digitalWrite(LED_RED,LOW);
    }

    
    if (digitalRead(BUTTON_BACK)==HIGH && back_flag){
        move_motor(-255);
        digitalWrite(LED_GRE,HIGH);
        digitalWrite(LED_RED,LOW);
        //Serial.println("backward button pressed");
    } 
    else if (digitalRead(BUTTON_FWRD)==HIGH && frwd_flag){
        move_motor(255);
        digitalWrite(LED_GRE,HIGH);
        digitalWrite(LED_RED,LOW);
        //Serial.println("Forward button pressed");
    } 
    else {
        move_motor(0);
        //digitalWrite(LED_RED,LOW);
        digitalWrite(LED_GRE,LOW);
    }

    delay(10);                       // Delay to space out tests
}

///////////////////////////////////////////////////////////////////
//Function Declaration. Do not change unless it's necessary
///////////////////////////////////////////////////////////////////
//void test_function(){
//    test_val = test_val + 1.00;
//    Serial.println(test_val);
//}


float get_pressure(void){
    // Read string from Slave
    //
    digitalWrite(LED_BUILTIN,HIGH);   // LED on
    Wire.beginTransmission(target);
    Wire.write(0xAA); // command to read pressure
    Wire.write((byte)0x00);
    Wire.write((byte)0x00);
    Wire.endTransmission();
        
    // Read from Slave
    Wire.requestFrom(target, (uint8_t)4); // Read from Slave 

    Wire.read(); // First byte is status indication, so for now we get rid of it from the buffer
    uint32_t ret;
    ret = Wire.read();
    ret <<= 8;
    ret |= Wire.read();
    ret <<= 8;
    ret |= Wire.read();
    psi = (ret - 1677722) * 25;
    psi /= (float)(15099494 - 1677722);
    //Serial.println(psi);

    digitalWrite(LED_BUILTIN,LOW);    // LED off
    delay(10);
    return;
}

void get_pos(void){
    pos_raw = analogRead(POT);
    pos = -0.00000000000127508008831955*pow(pos_raw, 5)+0.00000000281124191931775*pow(pos_raw, 4)-0.00000234010387463214*pow(pos_raw, 3)+0.000894194580794215*sq(pos_raw)-0.176725701121183*pos_raw + 99.6115709415247+0.37;
    pos = round(pos);
}

// Motor forward/backward
void move_motor(int pwm_duty){
    if (pwm_duty >= 0){
        analogWrite(MOTOR_PORT_A, 0);
        analogWrite(MOTOR_PORT_B, pwm_duty);
    } else{
        analogWrite(MOTOR_PORT_A, -pwm_duty);
        analogWrite(MOTOR_PORT_B, 0);
    }
}


// "move to" functions
void move_to_pressure(float target_psi){
    float psi_copy;
    noInterrupts();
    psi_copy = psi;
    interrupts();

    Serial.print("move to pressure: ");
    Serial.println(target_psi);

    float error = target_psi - psi_copy;
    Serial.println(error);
    float prev_error = 0;
    float sum = error;
    float rate;
    int timeout = 0;
    get_pos();
    while (abs(error) >= 0.1 && timeout < 140){
        noInterrupts();
        psi_copy = psi;
        interrupts();
        Serial.print(psi_copy);
        error = target_psi - psi_copy;
        Serial.println(error);
        rate = (error-prev_error)/0.01;
        int duty = int(kp_psi * error + ki_psi * sum + kd_psi * rate);
        if (duty > 255){duty = 255;}
        else if (duty < -255){duty = -255;}
        if ((duty > 0 && pos == 100.00)||(duty < 0 && pos == 0.00)){break;}
        move_motor(duty);
        prev_error = error;
        timeout++;
        get_pos();
        delay(50);
    }
    pressure_cmd.flag = false;
    Serial.println("Done");
    return;
}
void move_to_position(float target_pos){
    noInterrupts();
    Serial.print("move to position: ");
    Serial.println(target_pos);
    get_pos();
    float error = target_pos - pos;
    float prev_error = 0;
    float sum = error;
    float rate;
    int timeout = 0;
    while (abs(error) > 0.00 && timeout < 1000){
        get_pos();
        error = target_pos - pos;
        Serial.println(error);
        rate = (error-prev_error)/0.01;
        int duty = int(kp_pos * error + ki_pos * sum + kd_pos * rate);
        if (duty > 255){duty = 255;}
        else if (duty < -255){duty = -255;}
        move_motor(duty);
        prev_error = error;
        timeout++;
        delay(10);
    }
    Serial.println("Done");
    return;
}


//buffer to float conversion
float cmd_to_float(){
    int i = 0;
    while (Wire1.available()) { // slave may send less than requested
        psi_cmd_raw[i] = Wire1.read(); // receive a byte as character
        i++;
    };
    String pos_raw_string = String(psi_cmd_raw);
    return pos_raw_string.toFloat();
}

//
// handle Rx Event (incoming I2C data) as slave
//
void receiveEvent(size_t count)
{     
    //Serial.println("RECEIVED");
    Wire1.read(databuf_Rx, 1);  // copy Rx data to databuf_Tx
    switch (databuf_Rx[0]){
        case 'L' :
            move_to_position(cmd_to_float());
            break;
        case 'P' :
            pressure_cmd.flag = true;
            pressure_cmd.val = cmd_to_float();
            break;
    }
}

//
// handle Tx Event (outgoing I2C data) as slave
//
void requestEvent(void)
{
    //Serial.println(String(psi)+String(pos));
    Serial.println("sending request");
    (String(psi)+String(pos)).getBytes(databuf_Tx, MEM_LEN);  //converts psi to string, then copies it to the data buffer.
    Wire1.write(databuf_Tx, MEM_LEN);
    Serial.println("sent request");
}

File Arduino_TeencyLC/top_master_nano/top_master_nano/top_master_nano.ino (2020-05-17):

/* 
Adapted from Wire Master Reader by Nicholas Zambetti <http://www.zambetti.com>
Pneumatic Syringe System Master Test
This is the first working code (proof of concept) for the "big master" of the system, currently using an Arduino Nano.
This code reads pospsi_raw data which is sent from the "mid master". 
*/

#include <Wire.h>
#define MEM_LEN 32
#define INPUT_LEN 8
#define MAX_UNIT 20

char psi_raw[MEM_LEN]; //stores incomming pressure command temporarily
char pos_raw[MEM_LEN]; //stores incomming position command temporarily
char databuf_psi[MEM_LEN]; //stores outgoing char array temporarily
char databuf_pos[MEM_LEN];
char input[INPUT_LEN];
uint8_t ADDRESS[MAX_UNIT];

typedef struct {
    float psi;  //
    float pos;  //
} unit_data;
unit_data dataset[MAX_UNIT];

void setup() {
    Wire.begin();        // join i2c bus (address optional for master)
    Serial.begin(9600);  // start serial for output
    scan_address();
}

void loop() {

    String input_target;
    int target;
    String input_type;
    String input_value;

    if(Serial.available()){
        input_target = Serial.readStringUntil('-');
        target = input_target.toInt();
        input_type = Serial.readStringUntil('-');
        input_value = Serial.readStringUntil('\n');
        if (input_type == "g" || input_type == "G"){
            get_data(target);
            Serial.print("Unit#");
            Serial.print(target);
            Serial.print(" Pressure: ");
            Serial.print(dataset[target].psi); 
            Serial.print(" Position: "); 
            Serial.print(dataset[target].pos);
        } else if (input_type == "a" || input_type == "A"){
            get_hex_address(target);
        } else if (input_type == "l" || input_type == "L"){
            float input_cmd = input_value.toFloat();
            move_to_position(target,input_cmd);
        } else if (input_type == "p" || input_type == "P"){
            float input_cmd = input_value.toFloat();
            move_to_pressure(target,input_cmd);
        }
     Serial.println("");   
    }
    delay(10);
}

///////////////////////////////////////////////////////////////////
//Function Declaration. Do not change unless it's necessary
///////////////////////////////////////////////////////////////////

// Get data form all units once
void get_data_all(){   
    for (int j = 0; j < sizeof(ADDRESS); j++ ){
        if (ADDRESS[j] != 0){
            Wire.requestFrom(ADDRESS[j], 10);    // request X bytes from slave device

            int i = 0;
            while (Wire.available()) { // slave may send less than requested
                if (i < 5){
                    psi_raw[i] = Wire.read(); // receive a byte as character
                } else{
                    pos_raw[i-5] = Wire.read();
                }
                i++;
            }
            String psi_raw_string = String(psi_raw);
            String pos_raw_string = String(pos_raw);
            dataset[j].psi = psi_raw_string.toFloat();
            dataset[j].pos = pos_raw_string.toFloat();
        } else{
            break;
        }
    }
    return;    
}

// Get data from specific unit(num starts from 0)
void get_data(int unit_num){
    Wire.requestFrom(ADDRESS[unit_num], 10);    // request X bytes from slave device

    int i = 0;
    while (Wire.available()) { // slave may send less than requested
        if (i < 5){
            psi_raw[i] = Wire.read(); // receive a byte as character
        } else{
            pos_raw[i-5] = Wire.read();
        }
        i++;
    }
    String psi_raw_string = String(psi_raw);
    String pos_raw_string = String(pos_raw);
    dataset[unit_num].psi = psi_raw_string.toFloat();
    dataset[unit_num].pos = pos_raw_string.toFloat();
    return;
}

void get_hex_address(int addr){
    uint8_t ADD = ADDRESS[addr];
    Serial.print("0x");
    if (ADD < 16)
        Serial.print("0");
    Serial.println(ADD, HEX);
}

void move_to_pressure(int addr, float psi){
    if (psi >= 5.00 && psi <= 25.00){
        Serial.print("Unit#");
        Serial.print(addr);
        Serial.print(" to pressure: ");
        Serial.println(psi);
        String(psi).getBytes(databuf_psi, MEM_LEN);
        Wire.beginTransmission(ADDRESS[addr]); // transmit to device
        Wire.write("P");
        Wire.write(databuf_psi, MEM_LEN);
        Wire.endTransmission();
    }
}

void move_to_position(int addr, float pos){
    if (pos >= 0.00 && pos <= 100.00){
        Serial.print("Unit#");
        Serial.print(addr);
        Serial.print(" to position: ");
        Serial.println(pos);
        String(pos).getBytes(databuf_pos, MEM_LEN);
        Wire.beginTransmission(ADDRESS[addr]); // transmit to device
        Wire.write("L");
        Wire.write(databuf_pos, MEM_LEN);
        Wire.endTransmission();
    }
}

void scan_address(){
    
    byte error, address; //variable for error and I2C address
    int nDevices;
  
    Serial.println("Scanning...");
  
    nDevices = 0;
    for (address = 1; address < 127; address++ )
    {
        // The i2c_scanner uses the return value of
        // the Write.endTransmisstion to see if
        // a device did acknowledge to the address.
        Wire.beginTransmission(address);
        error = Wire.endTransmission();
    
        if (error == 0){
            Serial.print("Unit #");
            Serial.print(nDevices);
            Serial.print(" found at address 0x");
            ADDRESS[nDevices] = address;
            if (address < 16)
                Serial.print("0");
            Serial.println(address, HEX);
            nDevices++;
        }
        else if (error == 4){
            Serial.print("Unknown error at address 0x");
            if (address < 16)
                Serial.print("0");
            Serial.println(address, HEX);
        }
    }
    if (nDevices == 0){
        Serial.println("No I2C devices found, check connection and reboot?\n");
        while (1) {delay(10);}
    }    
    else{
        Serial.println("done\n");
    }
    delay(3000);
}

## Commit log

2020-04-02 updated code and journal
    [End Stop.SLDPRT, Housing_bottom_v05.STL, Housing_bottom_v06.STL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]
2020-04-23 V3 System Test
    [0415_bottom_clamp.3mf, 1x14femalepin.SLDPRT, 1x14malepin.SLDPRT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]
2020-04-25 version 3.1 models and journal
    [04-23.3mf, 04-25.3mf, TeensyLC_DRV8871_MPRLS_Qwiic_v01.kicad_pcb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]
2020-04-25 Revert "version 3.1 models and journal"
    This reverts commit 977644da9f5aa0aca8d70ec5670a792cd3697fd3.
    [3.5mm to npt.SLDPRT, End Stop.SLDPRT, Linear_sys_v01.SLDASM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]
2020-04-27 cleaned up uneccesary files
    [Worksheet in C Users 86182 Desktop Tufts _2020 Spring ME 0094 ME 0094 Journal(AutoRecovered).xlsx, housing_bottom_new.SLDPRT, housing_bottom_v06.STL]
2020-05-04 image test
    [04-27-Actuator Stand.3mf, Actuator Stand.SLDPRT, Actuator Stand.STL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]
2020-05-04 updated PCB
    [91292A110_TYPE 18-8 SS SOCKET HEAD CAP SCREW.SLDPRT, 91292A113_TYPE 18-8 SS SOCKET HEAD CAP SCREW.SLDPRT, 91292A115_TYPE 18-8 SS SOCKET HEAD CAP SCREW.SLDPRT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]
2020-05-05 moved CAD files out of the repo
    [04-23.3mf, 04-25.3mf, 04-27-Actuator Stand.3mf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]
2020-05-17 added instruction manual
    [BOM_Temp.xlsx, Worksheet in C Users 86182 Desktop Tufts _2020 Spring ME94 Backlog ME 0094 Journal.xlsx]
